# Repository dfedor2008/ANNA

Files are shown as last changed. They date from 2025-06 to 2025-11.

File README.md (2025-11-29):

# ANNA - High Altitude Rocket Computer

ANNA Banner

## Project Goal
Create a compact, affordable (under $100) and reliable rocket computer that can support both small and large-scale model rocket launches.

## How this project came to be
This rocket computer is part of a larger project: Moonstone. This project is a colaborative effort to launch a rocket off a High ALtitude Balloon. The link below is to slides which tell about the orgin of the project and other electronics which was done by me!!
https://docs.google.com/presentation/d/1WYTajgJSp5qMuNHan1WnkCnDspPzAP0AVPiKrxGjS5Q/edit?usp=sharing

## What is ANNA?
ANNA is a high-altitude rocket computer originally developed for a balloon-launched rocket project. It is designed to record key environmental and motion data during rocket flight, with plans to add telemetry and recovery features in future iterations.

Current features include:
- 3D orientation (gyroscope)
- Acceleration data
- Environmental measurements (temperature, pressure, humidity)
- MicroSD data logging
- Radio telemetry (in testing)

Future versions will include GPS and pyro channel support.

---

## Components

- **Microcontroller:** ATSAMD21G18A-A  
- **Radio Module:** SX1262 – Long-range, LoRa-based radio operating in the 915 MHz band  
- **Environmental Sensor:** BME280 – Measures temperature, pressure, and humidity  
- **IMU:** ICM-20948 – Provides 3D orientation and acceleration data  
- **Voltage Regulation:** AMS1117-3.3 – 3.3V linear regulator  
- **Storage:** MEM2061-01-188-00-A_REVA microSD slot

---

## Current Status *(as of 9/26/2025)*
-  Gyroscope (ICM-20948): Functional  
-  BME280 Sensor: Functional  
-  MicroSD Slot: Functional  
-  Power Regulation: Functional  
-  SX1262 Radio: Functional

---

## Features currently developed in new Board.
- **GPS Support:** For positioning and recovery  
- **Pyro Channels:** For recovery deployment and staging

---

## Radio Specification
The **SX1262** LoRa radio transmits in the 915 MHz ISM band. No HAM license is required in the U.S. to operate. So you don't need to have to pass any tests to operate it. It's inexpensive (~$3.50) and supports long-range two-way communication suitable for rocket telemetry.

---

## LED Behavior

| LED Pattern | Meaning |
|---|---|
| Blinking 0.5s ON / 0.5s OFF | All sensors are functioning |
| Blinking 0.9s ON / 0.1s OFF | At least one sensor failed to initialize |
| Off | Power issue / board not active |

---

## Setting Up ANNA

1. **Download Arduino IDE:**  
   https://www.arduino.cc/en/software

2. **Install SAMD Core:**  
   https://docs.arduino.cc/learn/starting-guide/cores/

3. **Download and upload the firmware** from this repository to ANNA.

4. **Connect the board** to your computer and select *Arduino Zero (Native USB Port)* as the target board.

---

## Contact
Have questions, want to donate, or just say Hi?  
 **dawid.fedor08@gmail.com**

---
## Circut Butler 

I want to thank Circuit Butler for sponsoring my project. They have been incredibly helpful, and without their support, my project wouldn’t have been able to be completed. Their fast PCB turnaround has allowed me to quickly test and iterate, which has been crucial to the development process. Additionally, whenever I had any questions, their response time was quick and their answers were always thorough and helpful. I highly recommend Circuit Butler to anyone looking for reliable and efficient PCBs!

---

## Special Thanks

- **Max Kendall** – For design, code, and logistics support  
- **Seth Kendall** – For logistics and general support  
- **Bob Phinney** – For project funding support  
- **Szymon Fedor** – For transportation and logistical help to Sci-Tech

---

## License

This project is released under GNU GENERAL PUBLIC LICENSE and CERN Open Hardware Licence Version 2 

## Pictures:

PXL_20250628_222645743 MP



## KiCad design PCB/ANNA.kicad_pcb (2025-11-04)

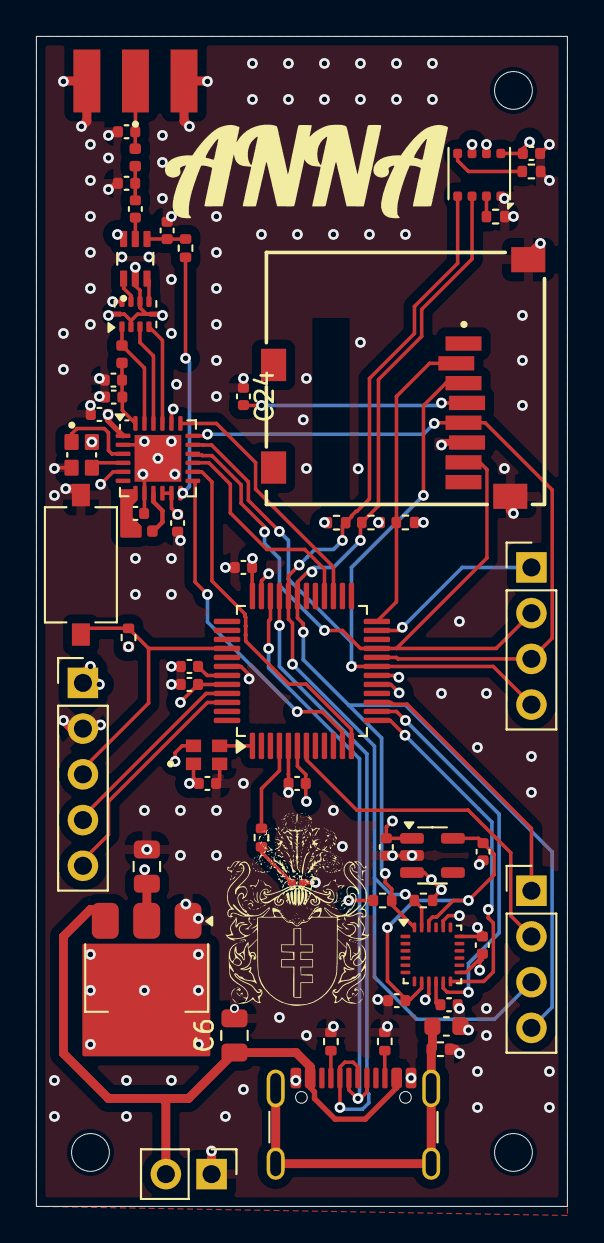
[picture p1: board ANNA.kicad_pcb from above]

Board: 4 copper layers, 29.5 x 65.0 mm, 62 parts (0 on the bottom side), 49 nets.

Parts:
C1: 4.7 nF; C_0603_1608Metric
C2, C8, C12, C25: 1uF; C_0402_1005Metric
C3, C9, C24: 100nF; C_0402_1005Metric
C4, C26: 100 nF; C_0402_1005Metric
C5: 10 uF; C_0402_1005Metric
C6, C13: 22u; C_0805_2012Metric
C7, C15: 1nF; C_0402_1005Metric
C10: 470nF; C_0402_1005Metric
C11, C14: 47pF; C_0402_1005Metric
C17, C18, C22: 0.1uF; C_0402_1005Metric
C21: 39pF; C_0402_1005Metric
C23, C27: 3.3pF; C_0402_1005Metric
D1: LED; LED_0201_0603Metric
FL1: 0900FM15K0039; Balun_Johanson_0900FM15K0039
H1, H2, H3: MountingHole_Pad; MountingHole_2.1mm
J1: USBC; USB_C_Receptacle_GCT_USB4105-xx-A_16P_TopMnt_Horizontal
J2: PinHeader_1x05_P2.54mm_Vertical
J3: POWER IN; PinHeader_1x02_P2.54mm_Vertical
J4, J5: PinHeader_1x04_P2.54mm_Vertical
Je1: Conn_Coaxial; RFSOLUTIONS_CON-SMA-EDGE-S
Jee1: GCT_MEM2061-01-188-00-A_REVA
L1: 15uH; L_0402_1005Metric
L2: 47nH; L_0402_1005Metric
L3: 9.1nH; L_0402_1005Metric
R1, R2, R11, R12: 10k; R_0402_1005Metric
R3: 1M; R_0402_1005Metric
R4: 300; R_0402_1005Metric
R5: 220; R_0402_1005Metric
R6, R7: 5k1; R_0402_1005Metric
R8: 100; R_0402_1005Metric
R10: 1K; R_0402_1005Metric
R13, R14: 1.8k; R_0402_1005Metric
SW1: RST; SW_Tactile_SPST_NO_Straight_CK_PTS636Sx25SMTRLFS
U1: ATSAMD21G18A-A; TQFP-48_7x7mm_P0.5mm
U2: AMS1117-3.3; SOT-223-3_TabPin2
U3: SX1262IMLTRT; QFN-24-1EP_4x4mm_P0.5mm_EP2.6x2.6mm
U4: MIC5504-1.8YM5; SOT-23-5
U5: PE4259
U7: ICM-20948; InvenSense_QFN-24_3x3mm_P0.4mm
U8: BME280; Bosch_LGA-8_3x3mm_P0.8mm_ClockwisePinNumbering
U9: ECS-327TXO-2012; OSC_ECS-327TXO-2012-33-TR
Y1: FA-128_32.0000MF20X-K5; OSCCC200X160X50

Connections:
+1V8: C12.1, C17.1, U4.5 (VOUT), U7.8 (VDDIO), U7.22 (~CS)
+3.3V: C3.2, C4.1, C5.1, C7.2, C8.1, C9.1, C13.1, C18.1, C24.2, C25.1, C26.2, J2.1, Jee1.4 (VDD), R1.1, R2.1, R5.2, R10.1, R13.2, R14.1, U1.6 (VDDANA), U1.17 (VDDIO), U1.36 (VDDIO), U1.44 (VDDIN), U2.2 (VO), U3.1 (VDD_IN), U3.10 (VBAT), U3.11 (VBAT_IO), U4.1 (VIN), U4.3 (EN), U5.6 (~CTRL/~VDD), U7.13 (VDD), U8.6 (VDDIO), U8.8 (VDD), U9.1 (EN), U9.4 (VDD)
A1: J4.2, U1.7 (PB08)
BUSY: U1.12 (PA07), U3.14 (BUSY)
CS_SD: Jee1.2 (CD/DAT3), R10.2, U1.24 (PA15)
D1: J4.1, U1.15 (PA10)
D2: J5.1, U1.23 (PA14)
D+: J1.A6 (D+), J1.B6 (D+), U1.34 (PA25)
D-: J1.A7 (D-), J1.B7 (D-), U1.33 (PA24)
DIO1: U1.11 (PA06), U3.13 (DIO1)
DIO_2: R8.2, U3.12 (DIO2)
FSYNC: U1.14 (PA09), U7.11 (FSYNC)
GND: C1.1, C2.2, C3.1, C4.2, C5.2, C6.2, C7.1, C8.2, C9.2, C10.2, C11.1, C12.2, C13.2, C14.1, C15.1, C17.2, C18.2, C22.2, C23.2, C24.1, C25.2, C26.1, C27.2, D1.1 (K), FL1.2 (GND), FL1.5 (GND), FL1.7 (GND), FL1.9 (GND), FL1.10 (GND), J1.A1 (GND), J1.A12 (GND), J1.B1 (GND), J1.B12 (GND), J2.2, J3.1, Je1.2 (Ext), Jee1.6 (VSS), Jee1.11 (GND), Jee1.12 (GND), R3.2, R6.1, R7.1, R11.2, R12.2, SW1.1, U1.5 (GNDANA), U1.18 (GND), U1.35 (GND), U1.42 (GND), U2.1 (GND), U3.2 (GND), U3.5 (GND), U3.8 (GND), U3.20 (GND), U3.25 (GND), U4.2 (GND), U5.2 (GND), U7.9 (SDO/AD0), U7.18 (GND), U7.20 (GND), U8.1 (GND), U8.7 (GND), U9.2 (GND), Y1.2 (GND), Y1.4 (GND)
INT1: U1.13 (PA08), U7.12 (INT1)
MISO: J5.2, Jee1.7 (DAT0), U1.21 (PA12), U3.16 (MISO)
MOSI: J5.4, Jee1.3 (CMD), U1.19 (PB10), U3.17 (MOSI)
NSS_1: U1.27 (PA18), U3.19 (NSS)
unnamed: C21.2, C23.1, L3.1
unnamed: D1.2 (A), R4.1
unnamed: FL1.3 (RFI_N), U3.22 (RFI_N)
unnamed: FL1.4 (RFI_P), U3.21 (RFI_P)
unnamed: FL1.1 (RFO), L2.1, U3.23 (RFO)
unnamed: FL1.6 (SW_RFI), U5.3 (RF2)
unnamed: FL1.8 (SW_RFO), U5.1 (RF1)
unnamed: J1.A5 (CC1), R6.2
unnamed: J1.B5 (CC2), R7.2
unnamed: C1.2, J1.S1 (SHIELD), R3.1
unnamed: C27.1, Je1.1 (In), L3.2
unnamed: R4.2, U1.4 (PA03)
unnamed: C2.1, U1.43 (VDDCORE)
unnamed: L1.1, U3.9 (DCC_SW)
unnamed: C10.1, L1.2, U3.7 (VREG)
unnamed: C11.2, C14.2, L2.2, U3.24 (VR_PA)
unnamed: C15.2, R8.1, U5.4 (CTRL)
unnamed: C21.1, U5.5 (RFC)
unnamed: C22.1, U7.10 (REGOUT)
unnamed: R12.1, U8.2 (CSB)
unnamed: R11.1, U8.5 (SDO)
Reset: U1.28 (PA19), U3.15 (~RESET)
SCK/CLK: J5.3, Jee1.5 (CLK), U1.20 (PB11), U3.18 (SCK)
SCL: J4.3, R2.2, R14.2, U1.32 (PA23), U7.23 (SCL/SCLK), U8.4 (SCK)
SDA: J4.4, R1.2, R13.1, U1.31 (PA22), U7.24 (SDA/SDI), U8.3 (SDI)
SWCLK: J2.4, U1.45 (PA30)
SWDIO: J2.5, U1.46 (PA31)
TCXO: U1.1 (PA00), U9.3 (OUTPUT)
VBUS: C6.1, J1.A4 (VBUS), J1.A9 (VBUS), J1.B4 (VBUS), J1.B9 (VBUS), J3.2, U2.3 (VI)
XTA: U3.3 (XTA), Y1.1 (IN)
XTB: U3.4 (XTB), Y1.3 (OUT)
nRST: J2.3, R5.1, SW1.2, U1.40 (~RESET)

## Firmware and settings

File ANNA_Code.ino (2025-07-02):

#include <Wire.h>
#include <Adafruit_Sensor.h>
#include <Adafruit_BME280.h>
#include <SPI.h>
#include <SD.h>
#include "ICM_20948.h"
#include <Scheduler.h>

#define WIRE_PORT Wire
#define Serial SerialUSB
#define AD0_VAL 0
#define SEALEVELPRESSURE_HPA (1013.25)
Adafruit_BME280 bme;

unsigned long delayTime;
Sd2Card card;
ICM_20948_I2C myICM;

const int chipSelect = 5;
void begining_led();
void set_up_led();
void problem_led();
void BME280();
void ICM20948();
void clearSDCard();
void make_Acel_file();
void make_BME_file();

bool SD_Card = false;
bool status_BME280 = false;
bool status_ICM20948 = false;
float sec_after_launch = 0;


void setup() {
  Scheduler.startLoop(loopsetup);
  PORT->Group[0].DIRSET.reg = (1 << 3);
  begining_led();
  Serial.begin(9600);
  while (!Serial)
    ;
  Serial.println();
  Serial.println("                            ANNA Project by Dawid Fedor");
  unsigned status;
  status = bme.begin(0x76);
  Serial.print("Initializing SD card...");
  if (!SD.begin(chipSelect)) {
    Serial.println("SD card initialization failed!");
    SD_Card = false;
  } else {
    Serial.println("SD card initialized.");
    clearSDCard();
    make_BME_file();
    make_Acel_file();

    SD_Card = true;
  }

  delay(1000);
  if (!status) {
    Serial.println("BME280 is not recognized");
  } else {
    Serial.println("BME280 is connected");
    status_BME280 = true;
  }
  WIRE_PORT.begin();
  WIRE_PORT.setClock(400000);

  bool initialized = false;
  while (!initialized) {
    myICM.begin(WIRE_PORT, AD0_VAL);

    if (myICM.status != ICM_20948_Stat_Ok) {
      Serial.println("Trying again...");
      delay(500);
    } else {
      initialized = true;
      status_ICM20948 = true;
    }
  }
  Serial.println("ICM20948 connected at 0x68 and initialized!");
  delay(1000);
}
void loop() {
  BME280();
  Serial.print("Sec after Launch:");
  Serial.println(sec_after_launch);
  ICM20948();
  delay(100);
  sec_after_launch=sec_after_launch+0.1;
}

void loopsetup() {
  set_up_led();
  if (SD_Card == false || status_BME280 == false || status_ICM20948 == false) {
    problem_led();
  }
}

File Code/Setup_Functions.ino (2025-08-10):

void begining_led() {
  for (int x = 0; x < 5; x++) {

    PORT->Group[0].OUTCLR.reg = (1 << 3);
    delay(100);
    PORT->Group[0].OUTSET.reg = (1 << 3);
    delay(100);
  }
}


void set_up_led() {
  PORT->Group[0].OUTSET.reg = (1 << 3);
  delay(500);

  // Set PA03 low
  PORT->Group[0].OUTCLR.reg = (1 << 3);
  delay(500);

  // Set PA03 low
}
void problem_led() {
  PORT->Group[0].OUTSET.reg = (1 << 3);
  delay(900);

  // Set PA03 low
  PORT->Group[0].OUTCLR.reg = (1 << 3);
  delay(100);
}

void start_functions() {
  Scheduler.startLoop(loopsetup);
  PORT->Group[0].DIRSET.reg = (1 << 3);
  PORT->Group[0].OUTCLR.reg = (1 << 3);
  rtc.begin(false);
  startTick = millis();
}
void time_keeping() {
  uint32_t nowTick = millis();
  elapsed = nowTick - startTick;

  Serial.print("Time since reset: ");
  Serial.print(elapsed / 1000);
  Serial.println(" s");
}

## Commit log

2025-06-11 Update and rename ANNA_Project_2.0.kicad_sch to ANNA_Project.kicad_sch
    [ANNA_Project.kicad_sch]
2025-06-29 Update and rename ANNA_Project_2.0.kicad_pcb to PCB/ANNA_Project_2.0.kicad_pcb
    [ANNA_Project_2.0.kicad_pcb]
2025-06-29 Update and rename ANNA_Project_2.0.kicad_sch to PCB/ANNA_Project_2.0.kicad_sch
    [ANNA_Project_2.0.kicad_sch]
2025-11-04 Update and rename ANNA (3).kicad_pcb to ANNA.kicad_pcb
    [ANNA.kicad_pcb]
2025-11-29 Revise current status and planned features in README
    Updated the current status and features in the README.
